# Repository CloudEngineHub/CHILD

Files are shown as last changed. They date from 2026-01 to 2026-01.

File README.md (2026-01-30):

## Overview
<!-- For hardware components and assembly details, please refer to [hardware](./hardware/README.md).   -->
For software installation, please refer to [Teleop_Instruction](./Teleop_Instruction.md).

## Hardware 
All hardware componenents are listed in the [BOM](./hardware/BOM.md) 
### Leader Assembly
Assembly timelapse video [link](https://www.youtube.com/watch?v=je-I6776OQc)  
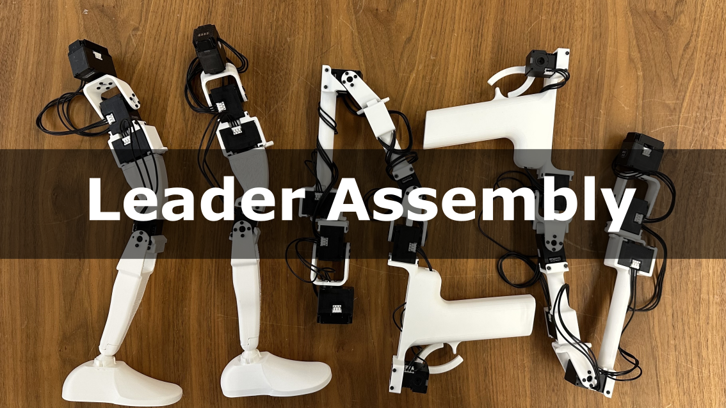
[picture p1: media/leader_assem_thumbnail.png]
[](https://www.youtube.com/watch?v=je-I6776OQc)  
Note:
- Motor horns should stay in zero position during assembly
- XL330-M288-T motors are used for the joints
- XL330-M077-T motors are used for the grippers
- Motors come with two size of screws: M2x6mm, and M2x8mm. 
- M2x6mm screws are used to attach 3D prints to the motor horns.
- M2x8mm screws are to attached 3D prints to motor body

### Torso Assembly
Assembly timelapse video [link](https://youtu.be/dCdK7ieb7UU)  
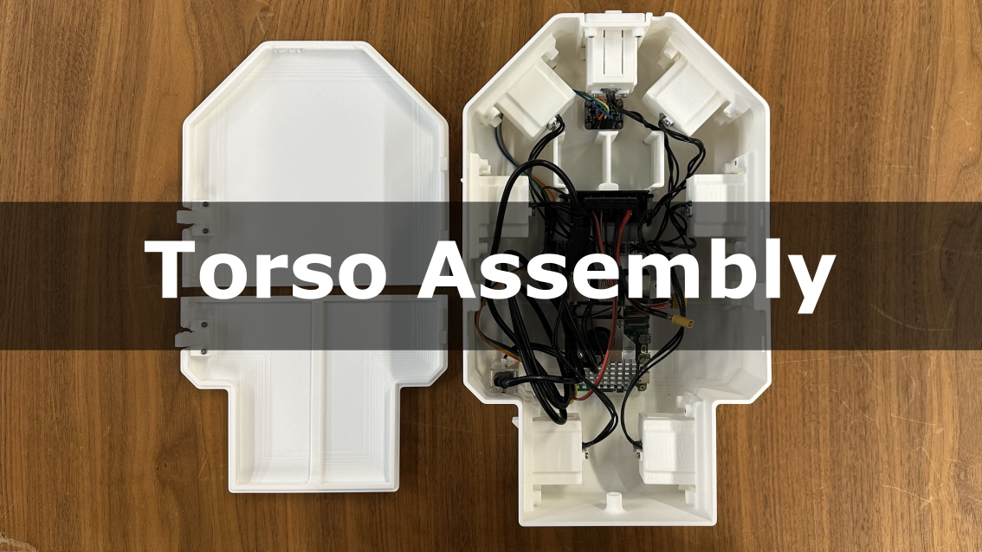
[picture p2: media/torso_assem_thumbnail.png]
[](https://youtu.be/dCdK7ieb7UU)
## To-Do
- \[✔️\] Release assembly guide.

## Citation
If you find this code useful in your research, please consider citing:
```
@INPROCEEDINGS{11203119,
  author={Myers, Noboru and Kwon, Obin and Yamsani, Sankalp and Kim, Joohyung},
  booktitle={2025 IEEE-RAS 24th International Conference on Humanoid Robots (Humanoids)}, 
  title={CHILD (Controller for Humanoid Imitation and Live Demonstration): A Whole-Body Humanoid Teleoperation System}, 
  year={2025},
  pages={1-6},
  }
```

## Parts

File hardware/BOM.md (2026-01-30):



# Schematic


# BOM
Items marked with `*` are optional for using pogo pin connectors
| Item | Quantity | Unit Cost (USD) | Cost | Source |  
| :--- | :---: | :---: | :---| :---|
| XL330-M288-T | 22 |  26.29 | $578.38 | [ROBOTIS](https://www.robotis.us/dynamixel-xl330-m288-t/)|
| XL330-M077-T | 2  |  26.29 | $52.58 | [ROBOTIS](https://www.robotis.us/dynamixel-xl330-m077-t/)|
| U2D2 | 1  |  35.31 | $35.31 | [ROBOTIS](https://www.robotis.us/u2d2/?srsltid=AfmBOopnAfcYD4wZJd2mYGfl02LkN3lmzDXwg2oOkg-FG9G7V-jAIUyt)|
| FPX330-H101 4pcs Set | 3  |  11.27 | $33.81 | [ROBOTIS](https://www.robotis.us/fpx330-h101-4pcs-set/)|
| TTL Expansion Board | 2  |  6.79 | $13.58 | [ROBOTIS](https://www.robotis.us/3p-jst-expansion-board/)|
| Raspberry Pi 5a | 1  |  80 | $80 | [Digikey](https://www.digikey.com/en/products/detail/raspberry-pi/SC1112/21658257)|
| Raspberry Pi 5 active cooler | 1  |  9.50 | $9.50 | [Sparkfun](https://www.sparkfun.com/raspberry-pi-active-cooler.html?src=raspberrypi)|
| Buck converter | 1  |  11.00 | $11.00 | [Amazon](https://a.co/d/34K1G3W)|
| Lipo batteries | 2  |  31.49 | $62.98 | [getfpv](https://www.getfpv.com/batteries/mini-quad-batteries/lumenier-850mah-4s-75c-lipo-battery-xt-30.html)|
| IMU | 1  |  34.95 | $34.95 | [Adafruit](https://www.adafruit.com/product/2472)|
| Baby Carrier | 1  |  37.99 | $37.99 | [Amazon](https://a.co/d/6YLBBi4)|
| XT30 Connector Female | 1  |  8.99 | $8.99 | [Amazon](https://a.co/d/beCXKoa)|
| SD card | 1  |  14.99 | $14.99 | [Amazon](https://a.co/d/bTOPJQl)|
| M3x8 screw | 33 |  0.0545 | $1.80 | [Mcmaster](https://www.mcmaster.com/91292A112/) |
| M2x8 screw | 4  |  0.0712 | $0.28 | [Mcmaster](https://www.mcmaster.com/91292a832/) |
| M2x6 screw | 24 |  0.0878 | $2.11 | [Mcmaster](https://www.mcmaster.com/91292a831/) |
| Female jumper wires | 6  |  0.0582 | $0.46 | [Amazon](https://a.co/d/gtiBsbT)|
| PLA Filament | 1.1kg  |  - | $22 | |
| Spring Piston 8pos* | 24 |  0.0878 | $2.11 | [DigiKey](https://www.digikey.com/en/products/detail/mill-max-manufacturing-corp/823-22-008-10-002101/1146974) |
| Spring Target 8pos* | 6  |  0.0582 | $0.46 | [Digikey](https://www.digikey.com/en/products/detail/mill-max-manufacturing-corp/419-10-208-00-006000/5176111)|
| CONN RCPT HSG 3POS 2.50MM* | 14 |  0.0448 | $1.12 | [DigiKey](https://www.digikey.com/en/products/detail/jst-sales-america-inc/EHR-3/527225) |
| 22-30AWG Crimp Tin* | 42 |  - | $2.52 | [DigiKey](https://www.digikey.com/en/products/detail/jst-sales-america-inc/SEH-001T-P0-6/26213194) |
| Custom PCB* | 14 |  - | $27 | [PCBWay](https://www.pcbway.com/) |
| | |  **Total** | $1000.71 ($1033.92*) | |

### Miscellaneous
- Power wires

# Torso
**3D Prints**
- [leader_mount](./3D_print_parts/leader_mount.STL) `x7` (Replace with [leader_mount_pogo_pin](./3D_print_parts/leader_mount_pogo_pin.STL) if using pogo pins)
- [back_cover_clip](./3D_print_parts/back_cover_clip.STL) `x2`
- [back_cover_lower](./3D_print_parts/back_cover_lower.STL)
- [back_cover_upper](./3D_print_parts/back_cover_upper.STL)
- [torso_lower](./3D_print_parts/torso_lower.STL)
- [torso_upper](./3D_print_parts/torso_upper.STL)
- [mount_pcb_clamp](./3D_print_parts/mount_pcb_clamp.STL) (If using pogo pins) `x7`

# G1 Limb Leaders
Screws and wires for leader assembly (included in XL330 servo box):
- M2x6mm self tapping screw
- M2x8mm self tapping screw
- TTL wires

**3D Prints**
- [G1_Arm_Leader_R_handle](./3D_print_parts/G1_Arm_Leader_R_handle.STL) `x2`
- [G1_Arm_Leader_trigger](./3D_print_parts/G1_Arm_Leader_trigger.STL) `x2`
- [G1_Leg_Leader_foot](./3D_print_parts/G1_Leg_Leader_foot.STL) `x2`
- [G1_Leg_Leader_knee_jnt_limit](./3D_print_parts/G1_Leg_Leader_knee_jnt_limit.STL) `x2`
- [G1_Leg_Leader_link_2](./3D_print_parts/G1_Leg_Leader_link_2.STL) `x2`
- [G1_Leg_Leader_link_3.1](./3D_print_parts/G1_Leg_Leader_link_3.1.STL) `x2`
- [G1_Leg_Leader_link_3.2](./3D_print_parts/G1_Leg_Leader_link_3.2.STL) `x2`
- [G1_Leg_Leader_link_4.1](./3D_print_parts/G1_Leg_Leader_link_4.1.STL) `x2`
- [G1_Leg_Leader_link_4.2](./3D_print_parts/G1_Leg_Leader_link_4.2.STL) `x2`
- [G1_Leg_Leader_L_link1](./3D_print_parts/G1_Leg_Leader_L_link1.STL)
- [G1_Leg_Leader_R_link1](./3D_print_parts/G1_Leg_Leader_R_link1.STL)
- [G1_Arm_Leader_L_link_1](./3D_print_parts/G1_Arm_Leader_L_link_1.STL)
- [G1_Arm_Leader_L_link_2](./3D_print_parts/G1_Arm_Leader_L_link_2.STL)
- [G1_Arm_Leader_L_link_3](./3D_print_parts/G1_Arm_Leader_L_link_3.STL)
- [G1_Arm_Leader_L_link_4](./3D_print_parts/G1_Arm_Leader_L_link_4.STL)
- [G1_Arm_Leader_L_link_5](./3D_print_parts/G1_Arm_Leader_L_link_5.STL)
- [G1_Arm_Leader_L_link_6](./3D_print_parts/G1_Arm_Leader_L_link_6.STL)
- [G1_Arm_Leader_R_link_1](./3D_print_parts/G1_Arm_Leader_R_link_1.STL)
- [G1_Arm_Leader_R_link_2](./3D_print_parts/G1_Arm_Leader_R_link_2.STL)
- [G1_Arm_Leader_R_link_3](./3D_print_parts/G1_Arm_Leader_R_link_3.STL)
- [G1_Arm_Leader_R_link_4](./3D_print_parts/G1_Arm_Leader_R_link_4.STL)
- [G1_Arm_Leader_R_link_5](./3D_print_parts/G1_Arm_Leader_R_link_5.STL)
- [G1_Arm_Leader_R_link_6](./3D_print_parts/G1_Arm_Leader_R_link_6.STL)
- [pogo_pin_adapter](./3D_print_parts/pogo_pin_adapter.STL) (If using pogo pins) `x4`
- [pogo_pin_pcb_spacer](./3D_print_parts/pogo_pin_pcb_spacer.STL) (If using pogo pins) `x4`

## Monitor Stand Adapter
- [Monitor_stand_attachment](./3D_print_parts/Monitor_stand_attachment.STL)
- [Monitor_stand_bracket](./3D_print_parts/Monitor_stand_bracket.STL)
- [monitor_stand_lock](./3D_print_parts/monitor_stand_lock.STL)

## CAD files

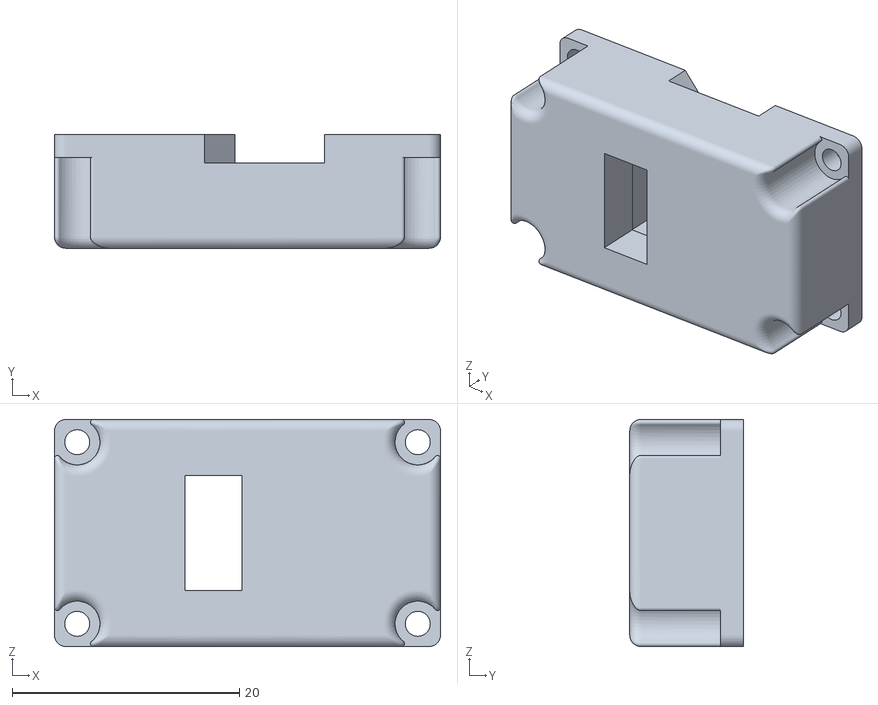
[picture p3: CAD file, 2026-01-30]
hardware/3D_print_parts/pogo_pin_adapter.STL
34.0 x 10.0 x 20.0

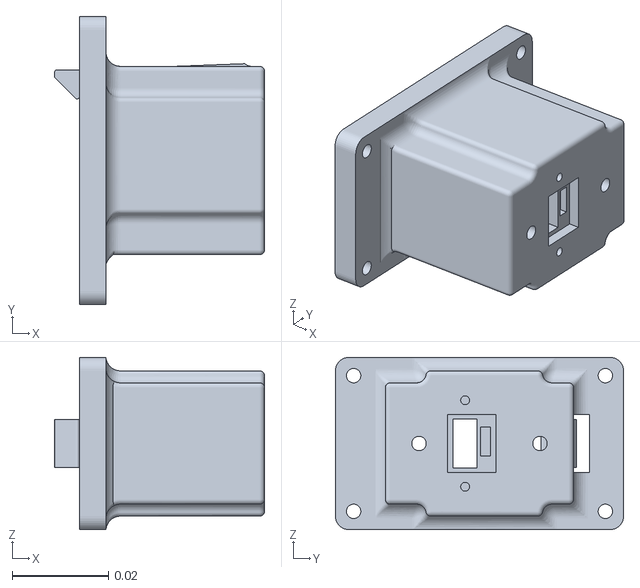
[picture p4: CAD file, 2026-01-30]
hardware/3D_print_parts/leader_mount_pogo_pin.STL
0.0437 x 0.06 x 0.0358

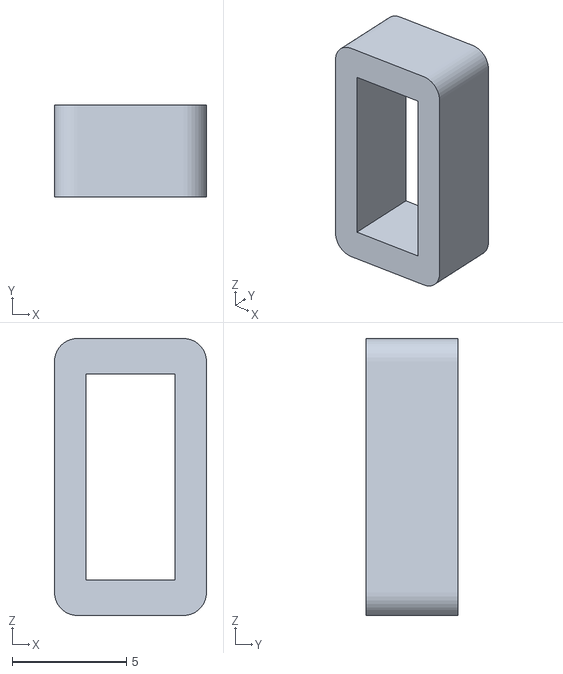
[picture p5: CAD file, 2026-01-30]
hardware/3D_print_parts/pogo_pin_pcb_spacer.STL
6.64 x 4.00 x 12.1

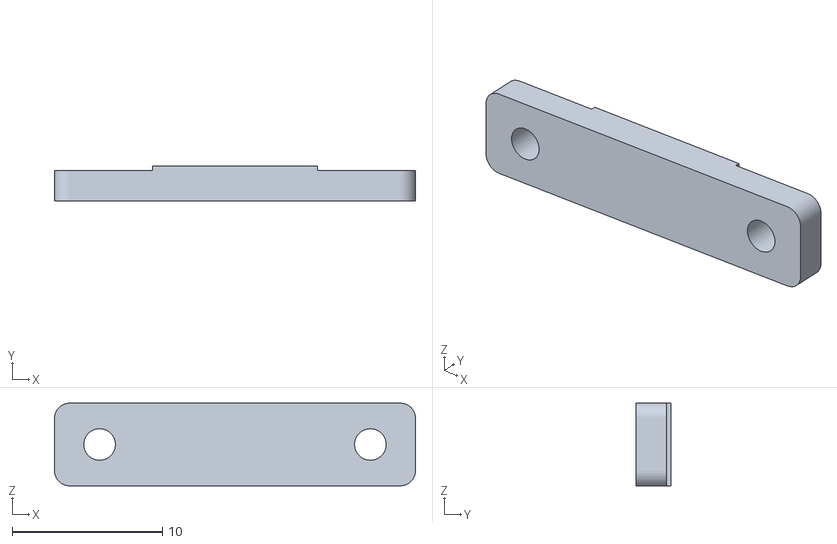
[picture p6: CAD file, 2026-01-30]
hardware/3D_print_parts/mount_pcb_clamp.STL
24.0 x 2.30 x 5.50
